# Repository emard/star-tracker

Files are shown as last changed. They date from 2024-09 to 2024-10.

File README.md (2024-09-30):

# star-tracker

Astrophotography motorized tripod that 
tracks objects on the sky as earth rotates.
DIY el-cheapo.

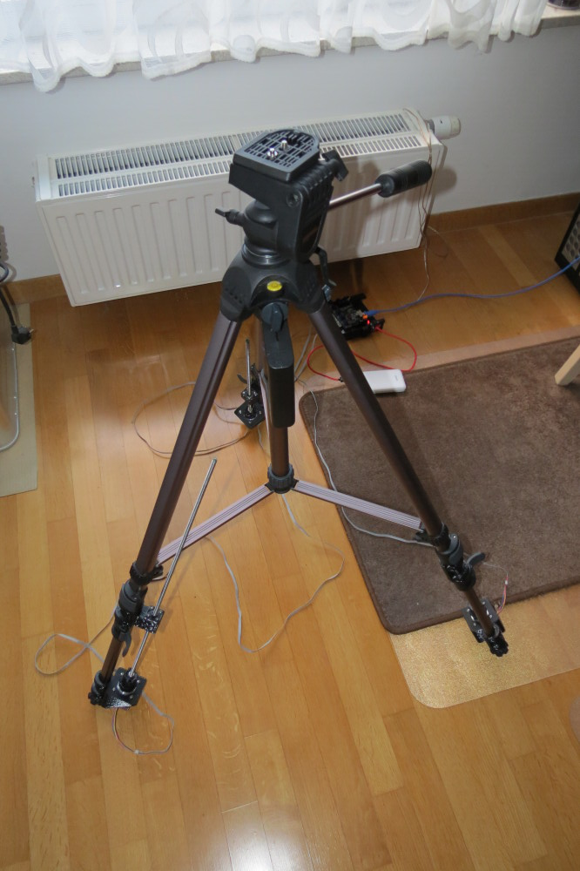
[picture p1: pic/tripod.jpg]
Tripod


3D printable parts fit 3 small step motors
with M6 threaded rods as linear actuators for
each of 3 legs of a cheap camera tripod
"Vanguard VT-528A".

Motors are controled by a 3D printer motherboard
"SKR 1.3" with Marlin firmware (g-code) powered
from USB lithium battery. When all 3 motors are
powered, motherboard draws about 2A, so 5V/10Ah
battery can last for about 5h.

Simple python code is used to stabilize the picture.
Code works without any knowledge of star/planet
positions, time, geolocation or hardware geometry
(tripod lengths and angles).

Usage:

Place tripod and set motor actuators to
a position from which each leg has enough
stroke to shorten or lengthen for tracking
objects.

Run "./keyboard.py" or "./joystick.py" code.
Motors will be driven to XYZ = 0,0,0 position
which considered as initial position.

Manually point telephoto lens to any object on the sky,
tighten it mechanically and apply maximum zoom.

Use keys Ins/Del, Home/End, Page UP/Down or
LEFT JOYSTICK X/Y and RIGHT JOYSTICK Y and SHIFT or
GREEN "A" BUTTON to center object in view.
Those control change length of each of 3 tripod legs.
Keys without SHIFT or GREEN "A" BUTTON make length change in steps of 0.1 mm,
Keys with SHIFT or GREEN "A" BUTTON do it in steps of 1 mm.

When object is in the center, press SPACE or LEFT TRIGGER.
Machine starts "learning".

As earth rotates, object moves from the center.

Use Ins/Del etc. keys or JOYSTICK to bring object to the center.
When object is in the center again, press RETURN or RIGHT TRIGGER

Machine will "learn" user's centering
and keep centering in the same direction.

If object still drifts slowly from the
center, bring it mantually to the center
and press RETURN or GREEN "A" BUTTON again.
Centering can be repeated any number of times and it
should refine.

BACKSPACE or RED "B" BUTTON cancels manual
centering done after the last RETURN or RIGHT TRIGGER.
After BACKSPACE or RED "B" BUTTON, motors wind back
to position in the direction learned from last RETURN
or RIGHT TRIGGER.

If long time has passed since last SPACE or LEFT TRIGGER
or camera is pointed to another object, press SPACE or
LEFT TRIGGER to start new learning and repeat manualy
centering and pressing RETURN.

ESC or BACK BUTTON returns motor to 0,0,0 position

0 or START BUTTON sets current position as 0,0,0

Press LEFT BUMPER and RIGHT BUMPER at the same time
to shutodown RPI (joystick.py only) so poweroff
can be done clean.

Happy star tracking

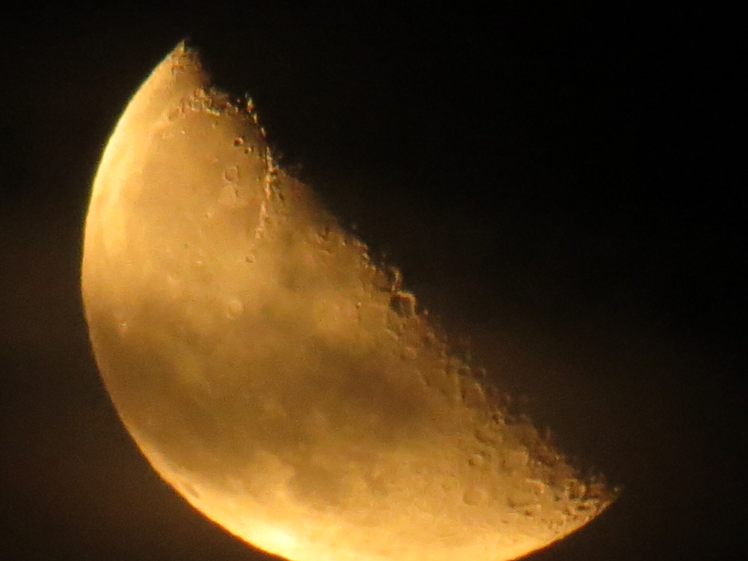
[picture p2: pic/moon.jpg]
Moon

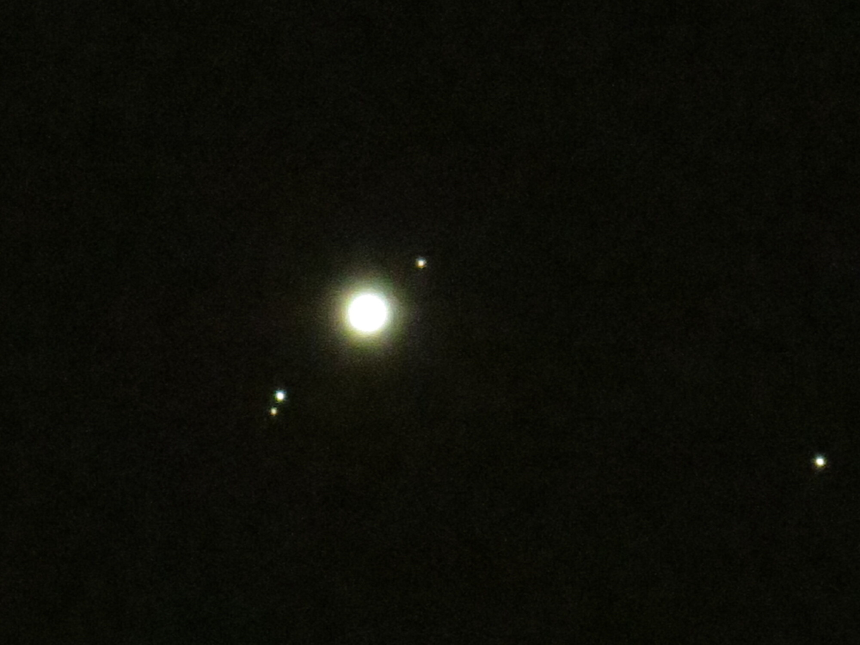
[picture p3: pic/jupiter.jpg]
Jupiter


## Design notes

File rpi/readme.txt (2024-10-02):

Download SD card image /tmp/2024-07-04-raspios-bookworm-armhf-lite.img.xz
unpack

unxz 2024-07-04-raspios-bookworm-armhf-lite.img.xz

check where is SD card

lsscsi

write image to SD card (be careful not to overwrite system disk)

dd if=2024-07-04-raspios-bookworm-armhf-lite.img of=/dev/sda

remove and insert SD card, mount vfat partition

mount /dev/sda1 /mt/usb/

Create a file named user userconf (or userconf.txt) containing the following:
pi:$6$c70VpvPsVNCG0YR5$l5vWWLsLko9Kj65gcQ8qvMkuOoRkEagI90qi3F/Y7rm8eNYZHW8CY6BOIKwMH7a3YYzZYL90zf304cAHLFaZE0
Place userconf (or userconf.txt) plus an empty file named ssh (or ssh.txt) in the BOOT (FAT32) partition of the SD card.
Insert the SD card in the Raspberry Pi and it should boot with access to user 'pi' (password : raspberry) via SSH.
@harphere

cd /mt/usb

echo "pi:$6$c70VpvPsVNCG0YR5$l5vWWLsLko9Kj65gcQ8qvMkuOoRkEagI90qi3F/Y7rm8eNYZHW8CY6BOIKwMH7a3YYzZYL90zf304cAHLFaZE0" > userconf.txt
touch ssh.txt

unmount and place SD card into raspberry

umount /dev/sdb1

power the raspberry, wait 1 minute to boot and login

ssh pi@raspberrypi.lan

copy files over the network

scp ../joystick.py 80-usbserial-startracker.rules startracker.service pi@raspberrypi.lan:~/

# for remote shooting from joystick blue btn:
# install chdk (1.6.1 known to work) and chdkptp raspbian (r964 known to work)
# chdkptp needs libusb 0.1
# apt install libusb-0.1-4

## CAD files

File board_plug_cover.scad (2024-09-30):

// mechanical protection
// for improvised plug to SKR 1.3 board

module inside_hole()
{
  cube([10,6,5.5],center=true);
}

module connector_holder()
{
  cube([17,16,7],center=true);
}

/*
module motor_wire_space()
{
  translate([0,11,0])
  cube([6.5,10,1.4],center=true);
}
*/

module solder_space()
{
  translate([0,7,0])
  cube([5*2.54,10,5.5],center=true);
}

module board_wire_space()
{
  translate([0,-6,0.5-0.01])
  cube([5,9,1.0],center=true);
}

module screw_in()
{
  for(i = [-1,1])
    translate([5*2.54/2*i,-5,-0.01])
      cylinder(d=1.8,h=3,$fn=12);
}

module screw_thru()
{
  for(i = [-1,1])
    translate([5*2.54/2*i,0,0.01])
      rotate([180,0,0])
        cylinder(d=3,h=10,$fn=12);
}

module motor_wire_holder(half=1)
{
  difference()
  {
    connector_holder();
    inside_hole();
    solder_space();
    board_wire_space();
    screw_in();
    screw_thru();
    translate([0,0,-50*half])
      cube([50,50,100],center=true);
  }
}

motor_wire_holder(half=1);

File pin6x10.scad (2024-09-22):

cylinder(d=6,h=10,$fn=32);

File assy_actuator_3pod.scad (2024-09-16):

include <clamp3pod.scad>
include <motor_holder.scad>
include <linactuator.scad>
/*---------------
size = 1.0; // small
// size = 1.2; // middle
for(i=[-1,1])
  translate([0,-i])
     print_clamp_half(i,size);
*/

actuator_pos = [-26,-30,  0];
actuator_rot = [  0,  0, 45];

module actuator_holder()
{
  difference()
  {
    translate([5,0,2])
    cube([35,25,4],center=true);
    cylinder(d=7,h=10,$fn=16,center=true);
    for(i=[-1,1])
      for(j=[-1,1])
        translate([i*15/2,j*15/2])
          cylinder(d=2,h=40,$fn=16,center=true);
  }
}

module actuator_holder_3pod()
{
  scal=1.2;
  // [[xyz pos], height],
  clamps =
  [
    [[0,0, 37  ],12],
    [[0,0, 21.5],19],
    [[0,0, 6   ],12],
  ];
  clamp_trans = [0,0,9];
  clamp1_rot = [180,0,0];
  difference()
  {
    union()
    {
    for(ct = clamps)
    translate(ct[0])
      rotate(clamp1_rot)
        {
          print_clamp_half(i=-1,size=scal,height=ct[1]);
        }
    translate(actuator_pos)
      rotate(actuator_rot)
        translate([0,0,14.15])
        rotate([180,0,0])
        linactuator();
        //actuator_holder();
      // holder reinforcement
      if(1)
      translate([-8,-12,12])
        rotate(actuator_rot)
        translate([-5.5,0,0])
        cube([20,25,24],center=true);
    }
    if(1)
    for(ct = clamps)
    translate(ct[0])
      rotate(clamp1_rot)
      rotate(clamp_rot)
      scale([scal,scal,1])
      translate(rod_pos)
          rod_profile(h=100,s=1);
  }
    
}

module actuator_clamp()
{
   scal=1.2;
   clamp1_rot = [180,0,0];
   rotate(clamp1_rot)
     print_clamp_half(i=1,size=scal,height=10);
}

//actuator_holder_3pod();
actuator_clamp();

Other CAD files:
assy_motor_3pod.scad
assy_motor_adapter.scad
clamp3pod.scad
connector_holder.scad
linactuator.scad
motor.scad
motor_holder.scad
nut_cutter.scad
print.scad
rod_holder.scad
sprocket_adapter_0.4n.scad
sprocket_adapter_0.8n.scad

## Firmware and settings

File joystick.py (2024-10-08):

#!/usr/bin/env python3

# apt install python3-serial python3-numpy python3-evdev

# https://python-evdev.readthedocs.io/en/latest/tutorial.html

# recommended tripod motor axis
#  Z
# X Y

from evdev import InputDevice, list_devices, ecodes, categorize
from select import select
from time import time
from serial import Serial
from os import system
import numpy as np

# joystick button have embossed labels
# joystick button name = os name
ABS_LX      = "ABS_X"
ABS_LY      = "ABS_Y"
ABS_RY      = "ABS_RZ"
HAT_X       = "ABS_HAT0X"  # set X direction
HAT_Y       = "ABS_HAT0Y"  # set Y direction
BTN_LT      = "BTN_BASE"   # mark object (start learning)
BTN_RT      = "BTN_BASE2"  # track object (from learning)
BTN_GREEN_A = "BTN_THUMB2" # faster (like SHIFT)
BTN_RED_B   = "BTN_THUMB"  # cancel manual
BTN_BLUE_X  = "BTN_TOP"    # shoot
BTN_BACK    = "BTN_BASE3"  # all axis back to 0
BTN_START   = "BTN_BASE4"  # set this position as new 0
BTN_LB      = "BTN_TOP2"   # shutdown RPI together LB & RB
BTN_RB      = "BTN_PINKIE" # shutdown RPI together LB & RB

# ABS_RX      = "ABS_RX" # not used
# BTN_YELLOW_Y = ["BTN_JOYSTICK", "BTN_TRIGGER"] # not used

# calculate next positions for auto and manual
def delta_position():
  global tp, st_track, st_manual
  tn = time()
  # tf is time in the future
  tf = tn  # [s] unix time float seconds since 1970
  tdelta = tf-tp
  tp = tf
  # delta position
  st_track  += st_speed_track  * tdelta/60
  st_manual += st_speed_manual * tdelta/60

def speed_limit():
  global st_speed_track, st_speed_manual
  for i in range(3):
    if st_speed_track[i] > max_speed:
      st_speed_track[i] = max_speed;
      print("limit track max")
    if st_speed_track[i] < -max_speed:
      st_speed_track[i] = -max_speed;
      print("limit track min")
    if st_speed_manual[i] > max_speed:
      st_speed_manual[i] = max_speed;
      print("limit manual max")
    if st_speed_manual[i] < -max_speed:
      st_speed_manual[i] = -max_speed;
      print("limit manual min")

# CNC functions

def drain():
  #return
  for line in cnc.readline():
    continue

def waitcomplete():
  #return
  cnc.write(b"M400\r")
  for line in cnc.readline():
    if line > 0 and line < 20: # probably "ok" response
      break
  drain()

def setorigin(x,y,z):
  cnc.write(b"G92 X%.2f Y%.2f Z%.2f\r" % (x,y,z))
  drain()

def position(x,y,z,feed):
  cnc.write(b"G1 X%.2f Y%.2f Z%.2f F%.2f\r" % (x,y,z,feed))
  drain()

# global 3D vectors for star tracking

st_before = np.array([ 0.0, 0.0, 0.0 ])
st_target = np.array([ 0.0, 0.0, 0.0 ])
st_memory = np.array([ 0.0, 0.0, 0.0 ])
st_delta  = np.array([ 0.0, 0.0, 0.0 ])

st_speed_track  = np.array([ 0.0, 0.0, 0.0 ])
st_speed_manual = np.array([ 0.0, 0.0, 0.0 ])

st_track  = np.array([ 0.0, 0.0, 0.0 ]) # auto tracking
st_manual = np.array([ 0.0, 0.0, 0.0 ]) # manual change


# timing

t_target  = 0
t_before  = 0
t_memory  = 0

# time when program started

t0 = time()
tp = t0
t  = t0

# max speed for each actuator
max_speed = 90 # [mm/min]
# max feed_rate for 3 actuators
max_feed_rate = 2*max_speed

# USB joystick

device_paths = ()
devices = [InputDevice(path) for path in list_devices()]
for device in devices:
    print(device.path, device.name, device.phys)
    if ecodes.EV_ABS in device.capabilities():
      # if "Joystick" in device.name:
        device_paths += (device.path,)

# A mapping of file descriptors (integers) to InputDevice instances.

# devices = map(InputDevice, ('/dev/input/event5', '/dev/input/event6'))
devices = map(InputDevice, device_paths)
devices = {dev.fd: dev for dev in devices}

for dev in devices.values(): print(dev)
# device /dev/input/event1, name "Dell Dell USB Keyboard", phys "usb-0000:00:12.1-2/input0"
# device /dev/input/event2, name "Logitech USB Laser Mouse", phys "usb-0000:00:12.0-2/input0"

# open and initialize CNC machine

cnc = Serial(port='/dev/ttyACM0', timeout=1)
#cnc = Serial(port='/dev/ttyS0', timeout=1)

waitcomplete()
cnc.write(b"M92 X1600 Y1600 Z1600\r") # 1600 steps per mm
drain()
cnc.write(b"M92\r")
drain()

# set currents max 800mA enough for 5V
cnc.write(b"M906 X800 Y800 Z800\r")
drain()

cnc.write(b"G90\r") # absolute mode
drain()
cnc.write(b"M18 S5 X Y Z\r") # release motor power after 5s idle
drain()
# turn green LED on
#cnc.write(b"M106\r")
#drain()

# star tracking loop globals

run = True
feed_faster = 0.0 # [mm/min] to finish early, feed faster
feed_factor = 1.0 # adjusts hardware feed to real time
step_time = 0.2 # [s] control recalculation time
position(0,0,0,max_feed_rate) # reset initial position
waitcomplete()
fast = 1
notify = "" # small printed message about btn control

# main loop reads joystick and periodically runs timed loop

select_timeout = 0.1 # [s] if no events return every 0.1 seconds
tnext = t0 # next timer event
# joystick ideal idle value should be 127 or 128
# but actually it fluctuates around 124-132
# so readings within this range should be ignored
flat_lo = 124
flat_hi = 132
# joystick exp/lin sensitivity
joy_exp = 0.05
joy_lin = 0.05
# fast factor with green btn (like shift) held
shift_fast = 4

left_bumper = 0
right_bumper = 0

# HAT is used to change direction of X and Y motors
# BUMPERs LEFT and RIGHT are used to change direction of Z motor
# here is default (negative values because for joystick Y
# axis are direction up as negative while we need direction up as positive
dir_x =  1
dir_y = -1
dir_z = -1

t_memory = t
st_memory = st_target.copy()
while True:
  r, w, x = select(devices, [], [], select_timeout)
  for fd in r:
    for event in devices[fd].read():
      # key pressed/released
      if event.type == ecodes.EV_KEY:
        keyevent = categorize(event)
        strtype = ecodes.bytype[keyevent.event.type][keyevent.event.code]
        #print(strtype)
        if strtype == BTN_LT and event.value > 0: # left trigger
          # start learning
          t_memory = t
          st_memory = st_target.copy()
          notify += "*"
        if strtype == BTN_RT and event.value > 0: # right trigger
          # apply learned tracking
          st_speed_track = (st_target - st_memory) / (t - t_memory) * 60
          st_track = st_target.copy()
          st_manual *= 0
          notify += ">"
        if strtype == BTN_BACK: # small btn left of big silver btn
          # return to zero position and stop
          st_manual *= 0
          st_track  *= 0
          st_speed_track *= 0
          st_target *= 0
          t_memory = t
          st_memory = st_target.copy()
          notify += "E"
        if strtype == BTN_START: # small btn right of big silver btn
          # set current position as new origin and stop
          setorigin(0,0,0)
          st_manual *= 0
          st_track  *= 0
          st_speed_track  *= 0
          st_target *= 0
          t_memory = t
          st_memory = st_target.copy()
          notify += "0"
        if strtype == BTN_RED_B: # red button "B" cancel manual move, return to tracking
          st_manual *= 0
          notify += "/"
        if strtype == BTN_GREEN_A: # green button "A", faster move (like shift)
          if event.value:
            fast = shift_fast
          else:
            fast = 1
        if strtype == BTN_BLUE_X: # blue button "X", shoot
          system("(sudo /home/pi/chdkptp/chdkptp.sh -c -erec; sudo /home/pi/chdkptp/chdkptp.sh -c -eshoot) &")
        if strtype == BTN_LB: # left bumper
          left_bumper = event.value
          dir_z = 1
        if strtype == BTN_RB: # right bumper
          right_bumper = event.value
          dir_z = -1
        if left_bumper > 0 and right_bumper > 0: # both left+right bumper = shutdown
          system("sudo poweroff")
      # analog paddles readings changed
      if event.type == ecodes.EV_ABS: # and (event.value < flat_lo or event.value > flat_hi):
        absevent = categorize(event) 
        strtype = ecodes.bytype[absevent.event.type][absevent.event.code]
        # print(strtype)
        axis = -1
        if strtype == ABS_LX: # left X
          axis = 0
          direction = dir_x
        # Y axis joystick (ABS_LY and ABS_RY) read out
        # negative value at up direction
        if strtype == ABS_LY: # left Y
          axis = 1
          direction = dir_y
        if strtype == ABS_RY: # right Y
          axis = 2
          direction = dir_z
        # "direction" is used to invert joystick axis
        # which is by default down positive
        # "direction" makes Y postive up
        # RX axis not used
        #if strtype == ABS_RX:
        #  print("RX", event.value)
        if strtype == HAT_X and event.value != 0:
          dir_x = event.value; # left -1, right 1
        if strtype == HAT_Y and event.value != 0:
          dir_y = event.value; # up -1, down 1
        if axis >= 0:
          st_speed_manual[axis] = 0
          if event.value <= flat_lo:
            st_speed_manual[axis] = np.exp(joy_exp * abs(event.value - flat_lo)) * np.sign(event.value - flat_lo) * direction * fast * joy_lin;
          if event.value >= flat_hi:
            st_speed_manual[axis] = np.exp(joy_exp * abs(event.value - flat_hi)) * np.sign(event.value - flat_hi) * direction * fast * joy_lin;

  # periodic timer
  t = time()
  if t > tnext:
    late = 0
    if t - tnext > 2*step_time: # we came too late, reschedule
      tnext = t + 1
      waitcomplete()
      late = 1
      print("late")
    tnext += step_time # next timer event every second
    speed_limit()
    delta_position()
    st_target = st_track + st_manual
    t_target = time()
    st_delta = st_target - st_before
    t_delta = t_target - t_before
    feed_rate = np.linalg.norm(st_delta) / t_delta * 60
    feed_rate = feed_rate*feed_factor+feed_faster+(1+10*late)
    if feed_rate > max_feed_rate:
      feed_rate = max_feed_rate
    x = st_target[0]
    y = st_target[1]
    z = st_target[2]
    position(x,y,z,feed_rate)
    report = "%+8.2f%+.1f%+8.2f%+.1f%+8.2f%+.1f %s" % (x,st_speed_track[0],y,st_speed_track[1],z,st_speed_track[2],notify)
    notify = ""
    print(report)
    st_before = st_target.copy()
    t_before = t_target

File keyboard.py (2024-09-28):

#!/usr/bin/env python3

# motor/leg position, mount tripod like this

#          E
#          X
#       N Z Y S
#          ^--- tripod handle
#          W
#      observer

# X (front) to east
# Y (right) to south west
# Z (left)  to north west

# keyboard controls

# manual position control

#                  Image move
# Insert     X++   down
# Delete     X--   up
# Home       Y++   up right
# End        Y--   down left
# Page Up    Z++   up left
# Page Down  Z--   down right

# manual speed control

#                  Image speed
# Q          Xs++  down
# A          Xs--  up
# W          Ys++  up right
# S          Ys--  down left
# E          Zs++  up left
# D          Zs--  down right

# automatic tracking

# SPACE      memorize this position when object is in the center
#            after a minute manually center same object with
#            Insert Delete Home End Page Up Page Down
#            when object is again in the center, press
# RETURN     to set speed to keep object in center
# BACKSPACE  to cancel manual settings, go back to auto position

import pygame
import serial
import time
import numpy as np
#from math import *

# time when program started
t0 = time.time()
tp = t0

st_before = np.array([ 0.0, 0.0, 0.0 ])
st_target = np.array([ 0.0, 0.0, 0.0 ])
st_memory = np.array([ 0.0, 0.0, 0.0 ])
st_delta  = np.array([ 0.0, 0.0, 0.0 ])

st_speed  = np.array([ 0.0, 0.0, 0.0 ])

st_track  = np.array([ 0.0, 0.0, 0.0 ]) # auto tracking
st_manual = np.array([ 0.0, 0.0, 0.0 ]) # manual change

t_target  = 0
t_before  = 0
t_memory  = 0

# read current unix time (UTC)
# and calculate motor target position
# for short time dt [s] in the future
# to generate next g-code
# returns: (X,Y,Z,F)
# XYZ [mm]     position
# F   [mm/min] feed rate (currently not working)
def calculate_future_position(dt):
  global tp
  tn = time.time()
  # tf is time in the future
  tf = tn + dt # [s] unix time float seconds since 1970
  tdelta = tf-tp
  tp = tf
  # next position
  st_next = st_target + st_speed * tdelta/60
  # compute feed rate
  feed_rate = np.linalg.norm(st_speed)
  # print("%8.2f %8.2f %8.2f %8.2f" % (st_next[0],st_next[1],st_next[2],st_next[3]))
  return (st_next, feed_rate)

def delta_position():
  global tp
  tn = time.time()
  # tf is time in the future
  tf = tn  # [s] unix time float seconds since 1970
  tdelta = tf-tp
  tp = tf
  # delta position
  return st_speed * tdelta/60

# simple functions

def drain():
  #return
  for line in cnc.readline():
    continue

def waitcomplete():
  #return
  cnc.write(b"M400\r")
  for line in cnc.readline():
    if line < 20: # probably "ok" response
      break
  drain()

def setorigin(x,y,z):
  cnc.write(b"G92 X%.2f Y%.2f Z%.2f\r" % (x,y,z))
  drain()

def position(x,y,z,feed):
  cnc.write(b"G1 X%.2f Y%.2f Z%.2f F%.2f\r" % (x,y,z,feed))
  drain()

def load_font():
        global font
        fontnames = [
            # Bold, Italic, Font name
            #(0, 0, "Bitstream Vera Sans Mono"),
            (0, 0, "DejaVu Sans Mono"),
            (0, 0, "Inconsolata"),
            (0, 0, "LucidaTypewriter"),
            (0, 0, "Lucida Typewriter"),
            (0, 0, "Terminus"),
            (0, 0, "Luxi Mono"),
            (1, 0, "Monospace"),
            (1, 0, "Courier New"),
            (1, 0, "Courier"),
        ]
        # TODO: Add a command-line parameter to change the size.
        # TODO: Maybe make this program flexible, let the window height define
        #       the actual font/circle size.
        fontsize     = 20
        circleheight = 10
        resolution   = (640, 480)
        # font = pygame.font.SysFont(fontnames, fontsize)
        for bold, italic, f in fontnames:
            try:
                filename = pygame.font.match_font(f, bold, italic)
                if filename:
                    font = pygame.font.Font(filename, fontsize)
                    print("Loaded font: %s (%s)" % (f, filename))
                    return
                    break
            except IOError as e:
                # print("Could not load font: %s (%s)" % (f, filename))
                pass
        else:
            font = pygame.font.Font(None, fontsize)
            # print("Loaded the default fallback font: %s" % pygame.font.get_default_font())

def textline(text, pos, color, linenumber=0):
        global font, background
        antialias = 1
        fontheight = font.get_linesize()
        window.blit(
            font.render(text, antialias, color, background),
            (pos[0], pos[1] + linenumber * fontheight)
            # I can access top-left coordinates of a Rect by indexes 0 and 1
        )

# main loop

cnc = serial.Serial(port='/dev/ttyACM0', timeout=1)
#cnc = serial.Serial(port='/dev/ttyS0', timeout=1)
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

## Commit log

2024-09-17 update 0.4mm sprocket adapter
    [sprocket_adapter_0.4mm_nozzle.scad]
2024-09-17 camera fixed to 2 legs
2024-09-18 turn on LED
2024-09-22 sprocket adapter with tube holder
    [sprocket_adapter_0.8mm_nozzle.scad]
2024-09-22 pin to hold tube firmly with sprocket adapter
    [pin6x10.scad]
2024-09-23 hardware accepts 2 digits like 1.23, 1/100 mm resolution
2024-09-24 tripod demo, some angle is changing with changing leg lengths, not sure is such model good enough to simulate real tripod, more testing is needed.
2024-09-25 cursors rework, prepare for "smart" tracking
    [cursors.py]
2024-09-26 prepare memory to reset manual control
    [cursors.py]
2024-09-26 use cnc device ttyACM0
2024-09-27 escape to stop tracking 0 to set current position to zero
2024-09-27 fix zero bug, text on graphic window
    [cursors.py]
2024-09-27 timer interrupt
2024-09-28 short notes how to boot raspberry
2024-09-29 covers for connectors
    [board_plug_cover.scad, connector_holder.scad]
2024-09-29 connector holder fix bugs
    [connector_holder.scad]
2024-09-30 connector holder - top version
    [connector_holder.scad]
2024-09-30 board connector, untested
    [board_plug_cover.scad]
2024-09-30 connector holder adjust dim's
    [connector_holder.scad]
2024-09-30 board plug, revert
    [board_plug_cover.scad]
2024-09-30 board plug adjust screw dist
    [board_plug_cover.scad]
2024-09-30 fix bug in manual scaling
    [joystick.py]
2024-09-30 board plug, screw hole reverted
    [board_plug_cover.scad]
2024-09-30 joystick fix stall bug
    [joystick.py]
2024-09-30 revert to tdelta, seems to provide smooth realtime response
    [joystick.py]
2024-10-06 call chdkptp.sh from background system("(chdkptp.sh ...) &") chdkptp.sh takes long time to complete, during that time python must continue executing for motors to keep turning
2024-10-08 joystick hat can invert x and y axis for more intuitive control
    [joystick.py]
2024-10-08 use bumpers to set direction of Z motor
